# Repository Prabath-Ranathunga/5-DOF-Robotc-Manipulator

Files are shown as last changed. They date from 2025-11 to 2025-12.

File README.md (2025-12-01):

# 5-DOF Robotic Manipulator

This repository contains the research, design, and implementation of a compact 5-degree-of-freedom (DOF) robotic manipulator. The project focuses on the complete development lifecycle, from initial design and simulation to the physical implementation and control of the robotic arm, making it suitable for rapid prototyping, research, and light-duty material handling applications.

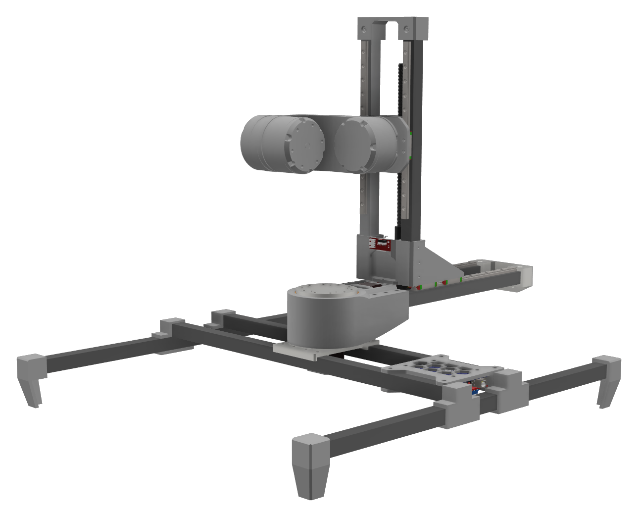
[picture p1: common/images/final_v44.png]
Robot final prototype design


## Little bit about project:
The development of a 5-DOF robotic manipulator, designed for versatility and precision in a compact form factor. The project encompasses the mechanical design using 3D-printed components to keep the manufacturing cost of this as low as possible. The manipulator's performance is validated through extensive simulation and a physical prototype, demonstrating its capabilities in tasks such as pick-and-place operations and path following. The results establish it as a viable and accessible platform for academic research, educational purposes, and light-duty industrial automation.

## Key Specifications

| Specification | Value |
| --- | --- |
| **Degrees of Freedom** | 5 |
| **Reach** | ~250mm |
| **Positional Accuracy**| ±1mm |
| **Frame Material** | 3D Printed PLA/PETG |
| **Control System** | Microcontroller-based |

## Design
The design of the robot arm itself based on 5-axis movements, to have very high levels of movement and accuracy. So its have three rotary axis and 2 linear axis. The speciality about this robot from others was the whole robot rotate around the workspace, so whatever its working on stays still. The main idea was to keep everything compact. 

The base axis called `R_360-axis`  is the main axis that rotate around the main platform while carrying all other axis and it holds whole weight of the robot arm. To get a smoother movement and reduce the axis play a triple cycloidal disk gear system was used instead of dual cycloidal disk design. Crossed roller slewing bearings are used in this design to reduce any friction on output housing. 

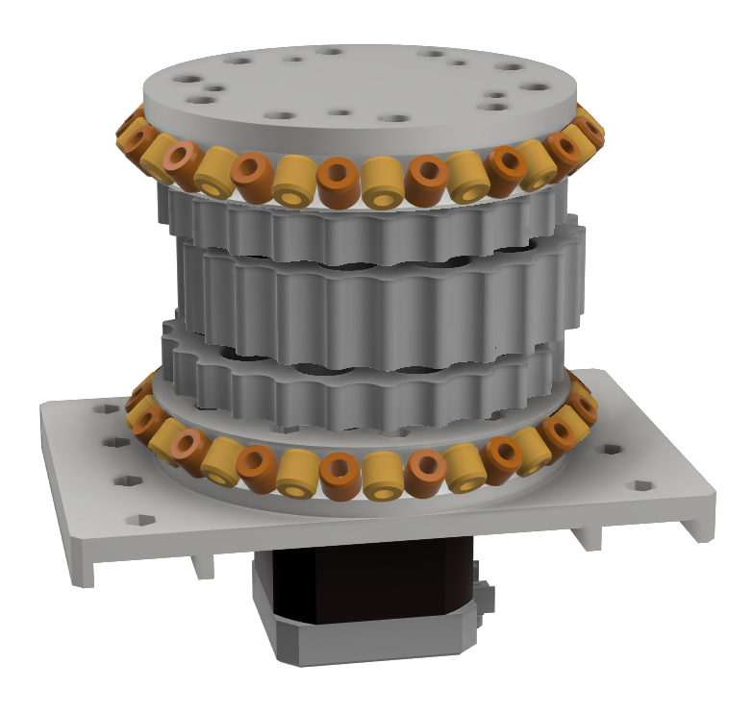
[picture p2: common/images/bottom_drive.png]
Rotary cyclodial drive with thiple disk


`R-axis` is linear axis that can vary the radius of robot arm movements and that uses motor rotary movements and converted into linear movement by mean of a lead screw and nut. To grain accurate smooth movements with ability to accommodate heavy axial loads, linear guide rails ware used to drive this axis. `Z-Axis` is also a linear axis that same as the `R-axis` but in vertically. This design also used linear guide rails and lead screw setup to drive the joint. `J-Axis` joint don’t have too much load. so, these joint uses two cycloidal disks instead of three cycloidal disks that attached to eccentric shaft to drive the joint. To carry all radial loads, two ball bearings were used in each side of the output housing. This `I-Axis` joint work same as the `J-Axis` joint. In this design main housing back plate is used to mount this joint component to the `J-Axis` arm.

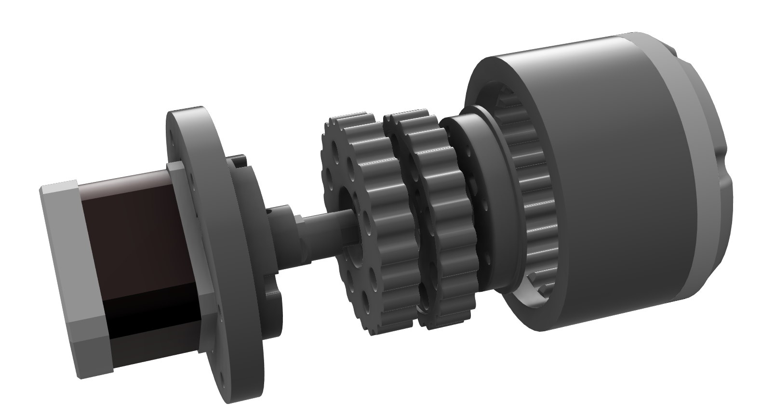
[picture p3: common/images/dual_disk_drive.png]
Rotary cyclodial drive with dual disk


There is a good explanation how to [design cyclodial drive in SOLIDWORKS](https://www.makerslide-machines.com/wp-content/uploads/2017/03/Building-a-Cycloidal-Drive-with-SOLIDWORKS.pdf) with all equations and tools that used for designing. CAD files available in [cycloidal drive CAD folder](common/cyclodial_drive/)

## Configuration
A modified version of Merlin 3D printer firmware for rotating bed based printers,[Marlin 360 Firmware](https://github.com/kory75/Marlin_360) was used to run the robot. Marlin firmware is mainly configured to 3-aixs 3D printers, To work with 5-axis manipulator, there have to do some configuration and modification to the firmware, Specifically both extruders were configured to run two rotary axis on tool head. The marlin firmware for polar coordinates works mainly with `X` and `Y` coordinates. The `Z` coordinates that receive from the G-code (Geometric Code) works independently with the `Z` axis. But the `X` and `Y` coordinates that the marlin firmware gets from the G-code sender is a cartesian coordinate system that represented by `X` and `Y` value. In the polar coordinating system using `𝑅_360(𝑋_𝐴𝑋𝐼𝑆)` and `𝑅(𝑌_𝐴𝑋𝐼𝑆)` coordinating values to move the axis motors and use to represent the `X` and `Y` cartesian coordinates. `R_360(𝑋_𝐴𝑋𝐼𝑆)` and `𝑅(𝑌_𝐴𝑋𝐼𝑆)` values are calculated from the cartesian coordinates, from a Gcode if needed. From the centre point of the working table or the bed of the machine `(x_0, y_0)` have to move at an angle of $\alpha$ to and the tool head have to move a difference in the radial direction `R` the machine. from the current orientation to destination orientation, 

**The angle difference $\alpha$ can be get by,**\
$`\alpha=\arctan\left(\frac{\text{destination}[Y]}{\text{destination}[X]}\right)-\arctan\left(\frac{\text{current}_{\text{cartesian}}[Y]}{\text{current}_{\text{cartesian}}[X]}\right)`$

**Radial distance `x_diff` difference can get by,**\
$`x_{\text{diff}} =
\sqrt{\text{destination}[X]^2 + \text{destination}[Y]^2}-\sqrt{\text{current}_{\text{cartesian}\_position}[X]^2 + \text{current}_{\text{cartesian}\_position}[Y]^2}`$

**Updating the rotary systems's `X-axis` length,**\
$`R_{360}(X\_{\text{AXIS}}) = R_{360}(X\_{\text{AXIS}}) + x_{\text{diff}}`$

**Using outer radius to compute new `Y` position,**\
$`\text{new\_target\_y} =(R_{360\_\text{OUTER\_RADIUS}} \cdot \alpha)+r_{360}[Y\_{\text{AXIS}}]`$

**Also, steps per units were calculated as,**\
$`\text{DEFAULT\_AXIS\_STEPS\_PER\_UNIT}(Y_{\text{AXIS}})=\frac{R_{360\_\text{STEPS\_PER\_ROTATION}}}{y_{\text{length}}}`$

This steps per units for the `y-axis` have to be very precise otherwise the output will be not as expected. so the default settings on marlin firmware need to override by this. 

## Electronics
For simplicity the whole build was based on Arduino MEGA with RAMPS shield and ESP module (I had few extra laying around me that time, initial plan was to use STM32 with custom board). For first test runs A4988 and DRV8825 drives user to run Nema-17 motors. ESP module connected to Arduino MEGA in one of serial port. and ESP module used as Wifi-Serial Bridge with [ESP-LINK](https://github.com/jeelabs/esp-link) installed in ESP. So the most of the electronic parts were come from 3D printer parts. 

## Simulation testing
Simulation or sort of simulation(didn't go through simulations since already building the prototype and most of movements was checked withing CAD design) was done with Simulink (MATLAB). There is a plugin call [simascape multibody link](https://uk.mathworks.com/help/smlink/ref/linking-and-unlinking-simmechanics-link-software-with-solidworks.html) that allow to export Solidworks CAD assemply models to Simscape multibody in Simulink.

## Prototyping 
Most of the parts in the machine are done by 3D printing, considering the requirements such as strength, price and printerbility, PETG was a great choice. The hard part of printing or prototyping is the gear-drive parts, since those cycodial parts have tight tollarance had to pring over and over again to test best fit to archive zero play(or very close to) drive. Other than that its mostly fitting parts together with M3 nuts & bolts and bunch of heat inserts. 
On final design there were vibrations in botton drive specially when arm is too far away from the center, one of the issue with lack of support on that radial axis and other one is bottom drive's bearing were also 3D printed ones, so its not a smooth ride even with lubrications. 

Robot final prototype image_01
Robot final prototype image_02
Robot final prototype image_03
Robot final prototype image_04
Robot final prototype image_05

## License
This publication is © 2022 [Prabath Ranathunga | ISSN 2961-502X].  
All rights reserved.

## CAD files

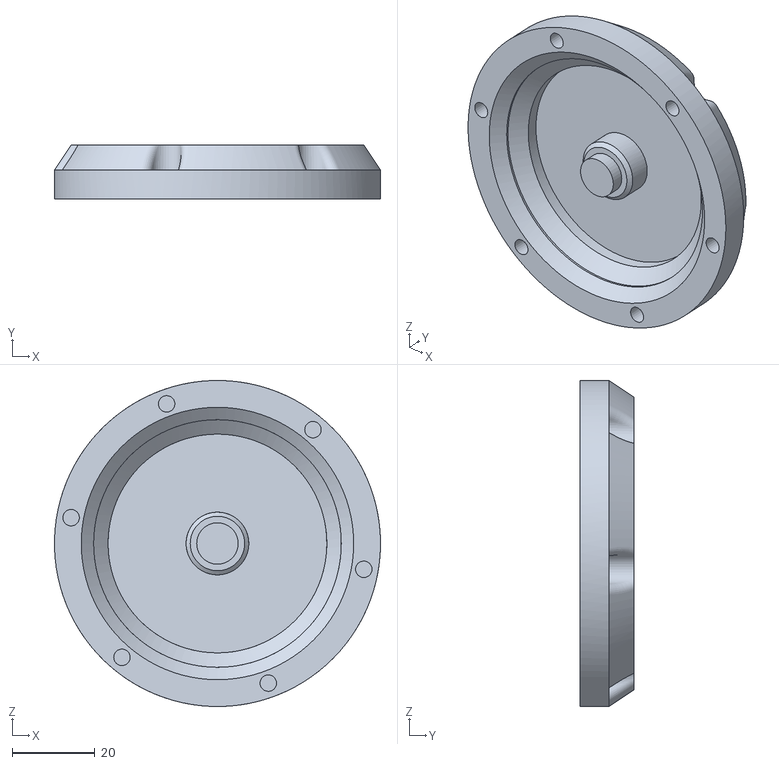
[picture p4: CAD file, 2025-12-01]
common/cyclodial_drive/top_cover.stl
79.0 x 13.0 x 79.0

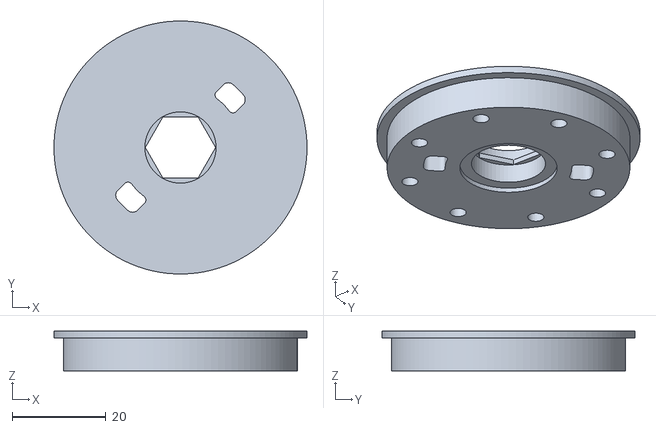
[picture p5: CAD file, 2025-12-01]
common/cyclodial_drive/top_plate.stl
54.0 x 54.0 x 8.50

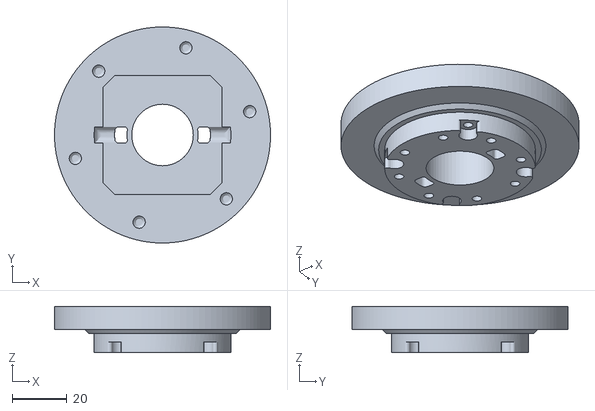
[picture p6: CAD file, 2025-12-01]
common/cyclodial_drive/base_and_stepper_mount.stl
79.0 x 79.0 x 17.0

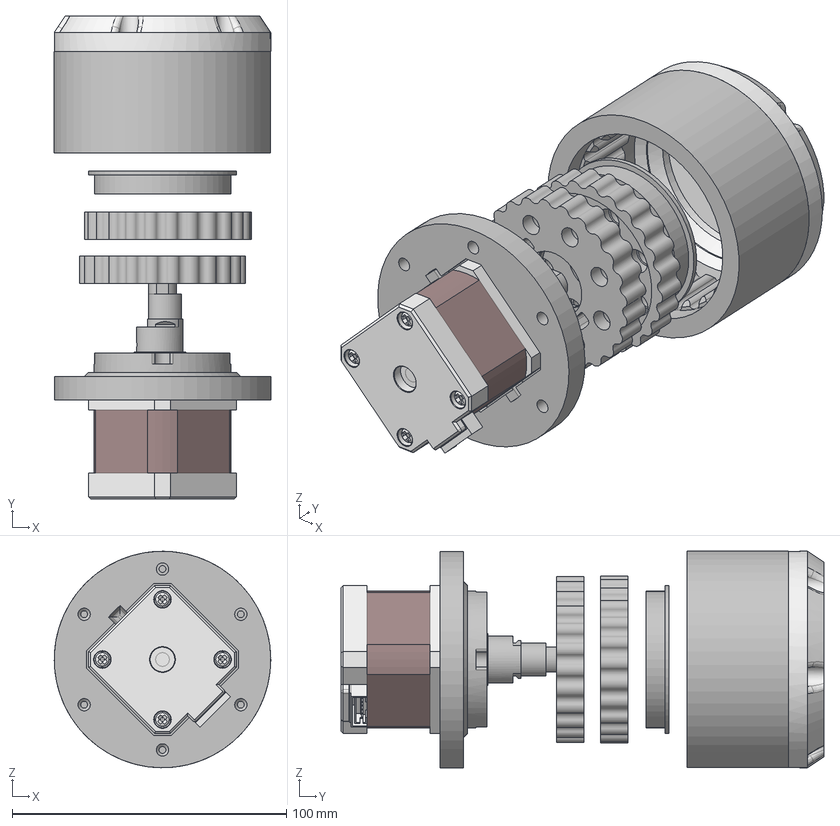
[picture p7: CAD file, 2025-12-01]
common/cyclodial_drive/cyclodial_drive.step
79.0 x 176.2 x 79.0 mm
top_plate
top_disk
bottom_disk
Ecc_Shaft v7
base_and_stepper_mount
SL42STH40-168MA-23
SL42STH40-168MA-23-V x 4
output_housing
top_cover

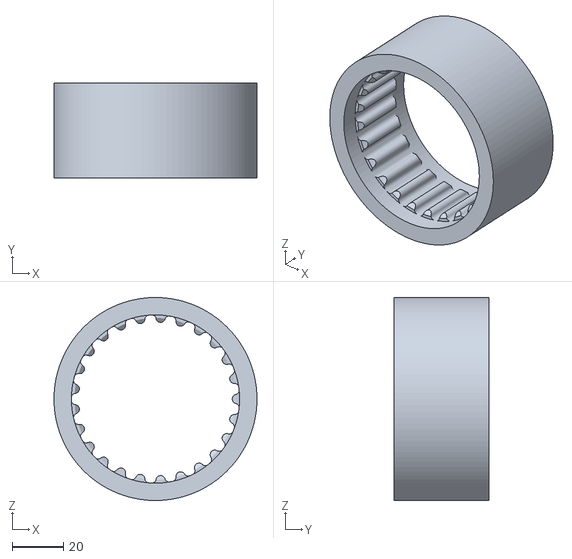
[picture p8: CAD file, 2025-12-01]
common/cyclodial_drive/output_housing.stl
79.0 x 37.0 x 79.0

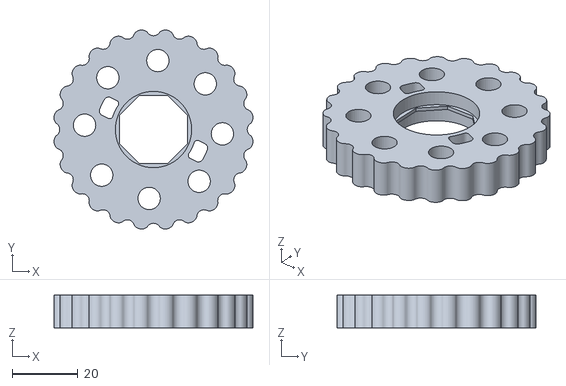
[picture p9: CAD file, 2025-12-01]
common/cyclodial_drive/bottom_disk.stl
60.5 x 60.5 x 10.0

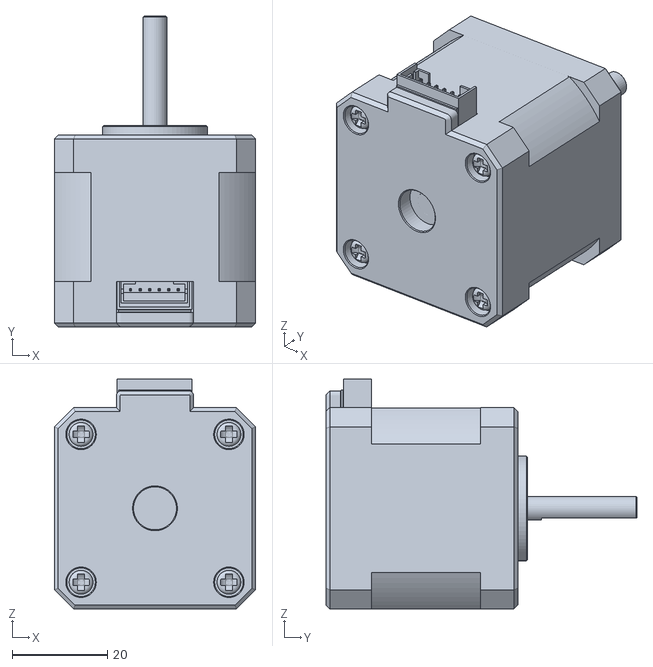
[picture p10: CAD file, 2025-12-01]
common/cyclodial_drive/nema_17.stl
42.2 x 65.2 x 48.2

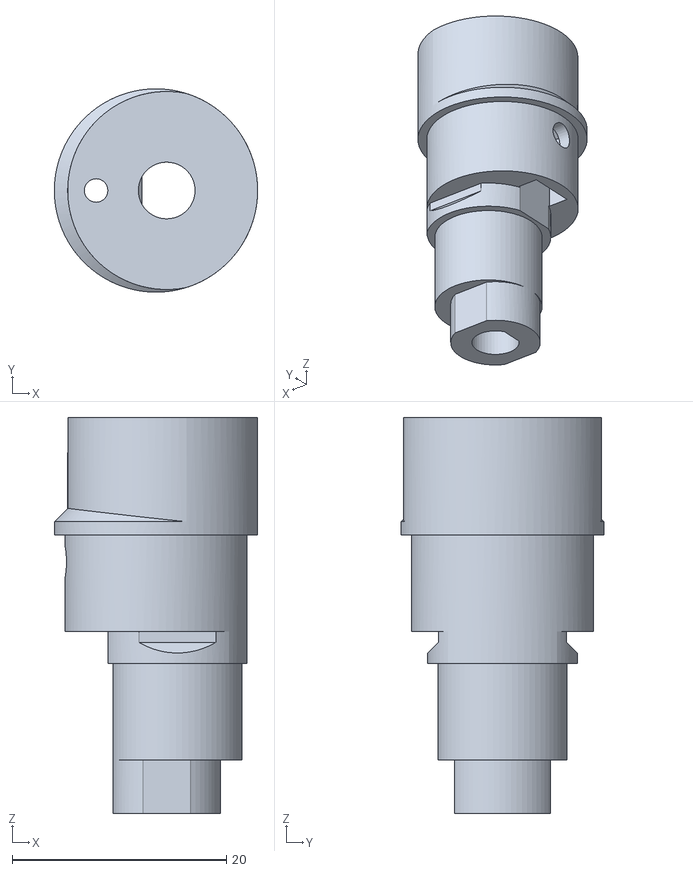
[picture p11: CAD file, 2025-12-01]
common/cyclodial_drive/ecc_shaft.stl
19.0 x 19.0 x 37.0

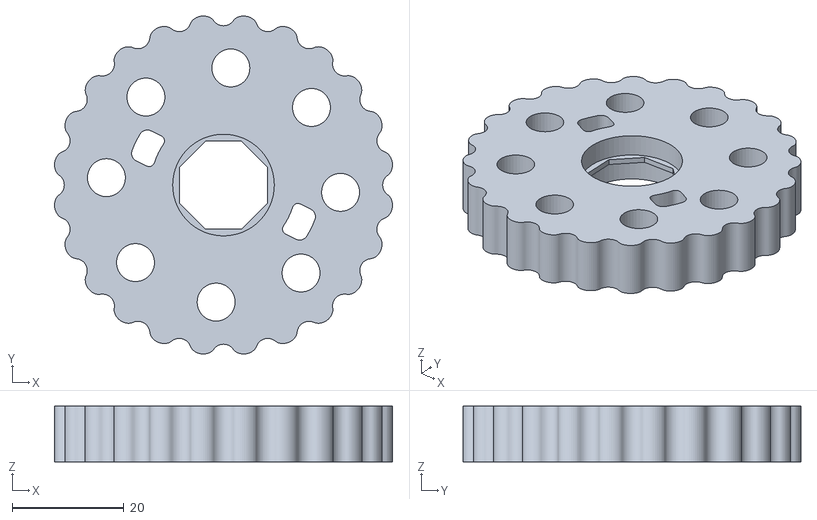
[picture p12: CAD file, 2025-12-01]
common/cyclodial_drive/top_disk.stl
60.5 x 60.5 x 10.0

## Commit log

2025-12-01 CAD files
    [base_and_stepper_mount.stl, bottom_disk.stl, cyclodial_drive.step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]
2025-12-01 Robot_arm stl
